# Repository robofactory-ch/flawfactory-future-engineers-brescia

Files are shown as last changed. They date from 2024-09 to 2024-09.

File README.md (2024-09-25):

# FlawFactory

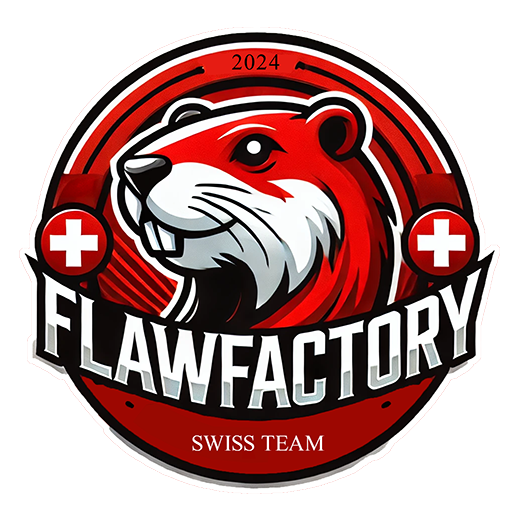
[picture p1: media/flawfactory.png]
FlawFactory Logo






**This is the github repository for team FlawFactory for WRO 2024 Brescia. You'll find our documentation in this readme**

We, Damian Hardegger and Jesse Born, make up the WRO team FlawFactory. We have been taking
part in WRO competitions for several years now. Previously, we competed in di erent teams in the
RoboMission category and were also successful there. But this year we took on a new challenge
and ventured into the Future Engineers task together as a joint team.

## Contents

- [Mobility and Hardware Design](#Mobility-Management)
- [Power and Sense Management](#Power-and-Sense-Management)
  - [Power Management](#Power-Management)
  - [Sense Management](#Sense-Management)
  - [Wiring Diagram](#Wiring-Diagram)
  - [Bill of Materials](#Bill-of-Materials)
- [Obstacle Management](#Obstacle-Management)
- [Photos](#Photos)
- [Videos](#Videos)
- [Enabling Reproducibility](#Enabling-Reproducibility)

<!-- Mobility management discussion should cover how the vehicle movements are managed. What motors are selected, how they are selected and implemented.
A brief discussion regarding the vehicle chassis design /selection can be provided as well as the mounting of all components to the vehicle chassis/structure. The discussion may include engineering principles such as speed, torque, power etc. usage. Building or assembly instructions can be provided together with 3D CAD files to 3D print parts. -->

## Mobility Management

The robot is built on a Lego chassis, which is supplemented where necessary with custom-designed 3D-printed components. These parts securely attach the motors and electronics to the chassis. The Lego structure incorporates dual Ackermann steering mechanism for both axles, allowing the robot to navigate tight turns with ease. To ensure even distribution of rotational power, we integrated a differential gear into each axle, powering all four wheels.

We connected the motors to the chassis using 3D-printed couplings that link the motor shaft directly to a Lego axle, allowing a single DC motor to drive the entire robot. The motor is positioned as low as possible to achieve a stable structure with a low center of gravity. We selected a 12V, 251 RPM motor with a 43.8:1 gearbox, which, despite its modest speed, is ideal for the robot due to its high torque of 18 kg\*cm at a stall current of 7A. This powerful motor allows for smooth driving and acceleration. The steering mechanism utilizes an RC servo motor with a stall torque of 15 kg\*cm, connected to the steering axle via a 3D-printed coupling and Lego gears. Since the DC motor obstructed the direct connection between the front and rear axles for simultaneous steering, we extended the linkage above the motor, placing the servo motor on top of the robot.

For the remaining electronics, we designed and printed additional parts. The camera mount is designed to allow the camera to be easily inserted from the top. The other electronics are mounted on a two-story plate, which is attached to the chassis using the classic Lego method of pushing axles through the 3D-printed parts and beams. We used standard M3 or M2.5 hardware to assemble the 3D-printed components and secure the electronics. The parts were designed to allow nuts to be pressed into place without support structures during printing, enabling a strong and reliable connection. Depending on accessibility, we used either square or hex nuts for the assembly.

<!-- Power and Sense management discussion should cover the power source for the vehicle as well as the sensors required to provide the vehicle with information to negotiate the different challenges. The discussion can include the reasons for selecting various sensors and how they are being used on the vehicle together with power consumption. The discussion could include a wiring diagram with BOM for the vehicle that includes all aspects of professional wiring diagrams. -->

## Power and Sense Management

### Power Management

We utilize a standard 4S LiPo battery as our power source. This versatile, off-the-shelf solution enables us to power both our drive and computer vision subsystems using a DC-DC buck converter. The 14.8V from the battery is directly fed into the H-Bridge motor driver, specifically an L298N variant. The buck converter provides a stable 5V supply to the main onboard computer, a Raspberry Pi 4B, which runs our computer vision algorithms. The 5V output is also routed to an Arduino Nano, connected via USB serial to the Raspberry Pi, to separate vision processing from motor control. The Arduino Nano handles tasks such as acceleration and PWM modulation.

Power consumption was a significant consideration, as the Raspberry Pi can draw up to 1.2 amps, and the servo motor can pull up to 4A in a stall situation. The DC-DC converter was selected to meet these requirements. The drive motor, powered separately, can draw up to 7A. By separating the power sources, only the H-Bridge needed to be rated for these high currents.

Due to cost considerations, we selected an H-Bridge with a current rating below the stall current, necessitating gradual acceleration to avoid damage—a lesson learned through experience. The H-Bridge allows the Arduino Nano to control the motor with three pins: two for selecting the direction of rotation and one for moderating speed using PWM (pulse width modulation). This setup ensures that the 12V system can be safely controlled using the 5V logic from the Raspberry Pi and Arduino.

### Sense Management

For the regional finals, we experimented with various sensors, including ultrasonic sensors, gyroscopes, and cameras. Through our trials, we discovered that a camera alone suffices, provided it has a sufficiently wide field of view. Consequently, we selected a Pi HQ camera equipped with a screw-on lens offering a 120° field of view. This camera allows the robot to accurately perceive its surroundings.

The Pi HQ camera connects directly to the Raspberry Pi, drawing power from the Pi itself, which is supplied via the 5V pins on the GPIO connector. Based on our experiences at the regional finals, we decided to eliminate all ultrasonic sensors and the gyroscope. Instead of relying on hardware sensors, we opted to enhance video processing to emulate distance sensing. To facilitate this and improve wall detection robustness, we mounted the camera precisely 100 mm above the ground, aligning its centerline with the top edge of the walls. This allows us to crop the image to a fixed height, ensuring that the walls are always detected at the same height in the image.

### Wiring Diagram

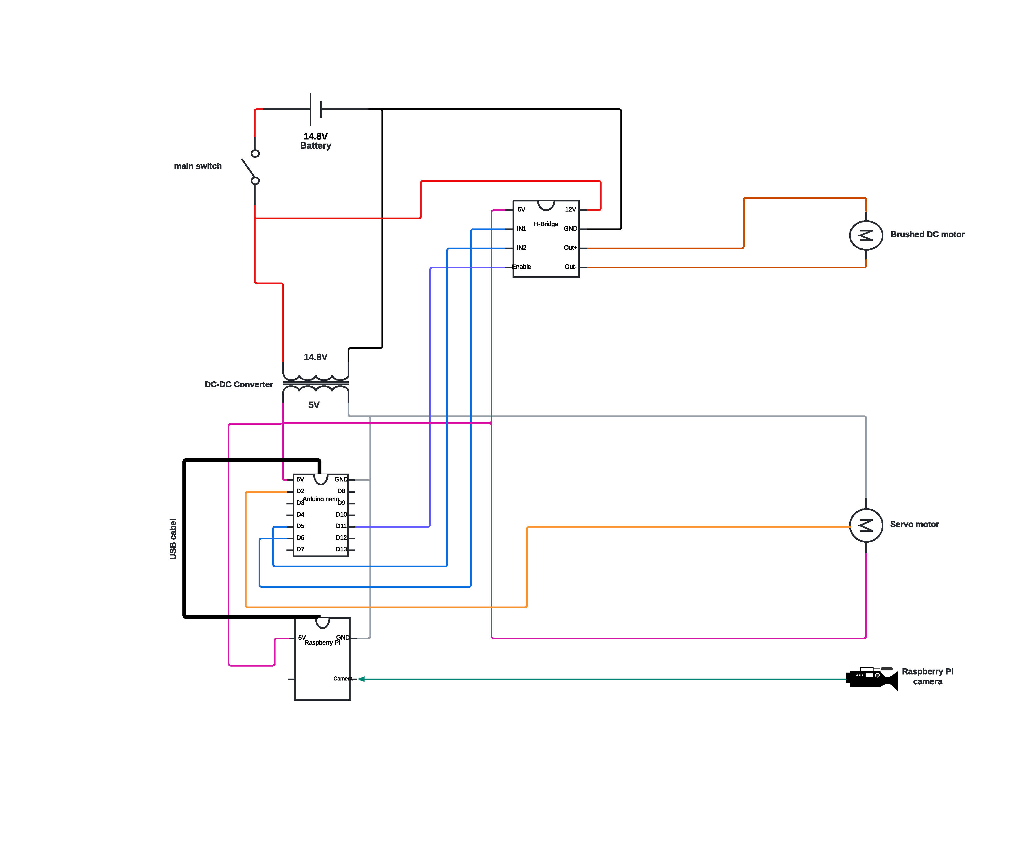
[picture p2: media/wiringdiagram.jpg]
Wiring Diagram


### Bill of Materials

| Amount | Product | Price in Swiss Francs (CHF 1.00 ~ USD 1.18) |
| --- | --- | --- |
| 1 | Raspberry Pi M12 HQ Camera | CHF 45.34 |
| 1 | EDATEC 12MP 3.2mm M12 Raspberry | CHF 28.84 |
| 1 | Raspberry Pi 4 Model B 8GB | CHF 79.00 |
| 1 | Arduino Nano: Multifunktionales Board ATmega328 16Mhz, Mini-USB | CHF 19.95 |
| 1 | Tattu LiPo-Akku 14.8V 850mAh 95C 4S1P RL | CHF 14.00 |
| 1 | L298N Schrittmotorendstufe / H-Brücke / DC Motor Treiber | CHF 8.90 |
| 1 | PDI-5515MG Digital Standard Servo 15.32Kg\*cm | CHF 18.90 |
| 1 | 12V 251RPM 18Kg\*cm DC Getriebemotor mit Encoder | CHF 35.90 |
| ca. 20 pieces | M2.5 Screws and nuts | CHF 2.00 |
| ca. 10 pieces | M2 Screws and nuts | CHF 1.00 |
| ca. 300g | 3D printing filament | CHF 5.00 |
| ca 20 pieces | Jumpercabel | CHF 4.00 |
| See stud.io file | LEGO technic bricks | |
| 4 | LEGO technic wheels | |
| **TOTAL** | | **CHF 262.83** |

<!-- Obstacle management discussion should include the strategy for the vehicle to negotiate the obstacle course for all the challenges. This could include flow diagrams, pseudo code and source code with detailed comments. -->

All files for the 3D printed parts can be found in the [3D-Printed-Parts](/cad/3d) folder. All parts can be printed without supports at 0.2mm layer height. we recommend using PET-G or nGen for the parts (PLA can also be used).
The wiring diagram can be found in the [Wiring Diagram](/media/wiringdiagram.jpg) file. The instructions for the LEGO chassis can be found in the [stud.io file](/cad/future_eng_flawfactory_v2.io).

## Obstacle Management

### Opening Race

The robot's behavior is modeled using a behavior tree. The [StateMachine](/raspy/statemachine.py) class manages the current state and handles transitions to new states. States can also be scheduled to start in the future, which is useful for delaying turns to avoid hitting inner walls. In the opening race, we use the states “STARTING,” “PD-CENTER,” “TURNING-L/R,” and “DONE.”

We begin by determining the round direction. First, we crop the top half of the image and filter out all black pixels using OpenCV's `cv2.inRange` function. On this Boolean map of black pixels, we detect edges using `cv2.Canny`. By applying `np.argmax`, we find the heights of the walls in pixels at each x-coordinate in the image. The discrete differences between these heights are calculated using `np.diff`, raised to the fourth power, and summed up. This helps us identify the jump in wall height when the inner wall first appears.

For driving, we employ a PD-Controller. The input is derived from the black portion of a region-of-interest extracted from the outer edges of the black-and-white Boolean image. This is compared to a pre-calibrated fixed portion. We follow only the outer wall to avoid collisions with the inner walls, especially if their gap distance is randomized to be small.

Using a small region of interest in the center of the camera feed, we detect the blue and orange lines on the game mat. The color image is converted to HSV for this purpose. Upon encountering such a line, depending on its color, we initiate a turn and decrement the remaining corners counter, allowing us to accurately stop at the end of the round.

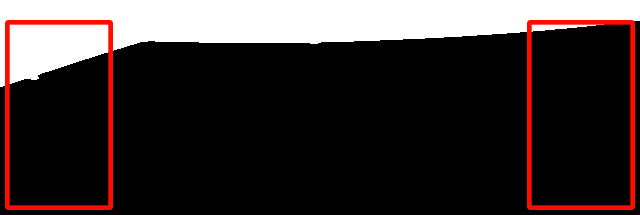
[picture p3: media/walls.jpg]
Wall Detection


The red outlines show the region of interest used for wall detection.

### Obstacle Race

In addition to extracting a black-and-white image, we convert the cropped color image to HSV. This conversion allows us to more easily and robustly extract red and green pixels. We then use `cv2.Canny` and `cv2.findContours` to search for contours in this image. The centroids of the contours are extracted and stored along with their width and height. The behavior tree is updated with two new states: "TRACKING-PILLAR" and "AVOIDING-PILLAR-R/G".

When handling the HSV color space, special care is needed for colors near the red hue due to the wrap-around effect. The hue value for red is around 0° and 360°, meaning it wraps around the HSV color wheel. To accurately detect red, we create two separate masks: one for the lower range (e.g., 0° to 10°) and another for the upper range (e.g., 350° to 360°). These masks are then combined to form a single mask that accurately captures all red hues. This approach ensures that all shades of red are detected, avoiding issues caused by the hue value wrapping around the color wheel.

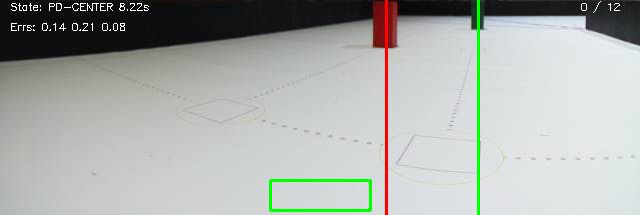
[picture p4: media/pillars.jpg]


In the image above you can see the robot detecting the red and green pillars. After processing the image, the program returns a list of found pillars, sorted by their distance to the robot. The robot then drives towards the closest pillar, until it is close enough to the pillar to avoid it. The robot then drives around the pillar and continues to the next one. You can also see the center ROI used for detecting turn marking lines.

<!-- Insert image with behavior tree here -->

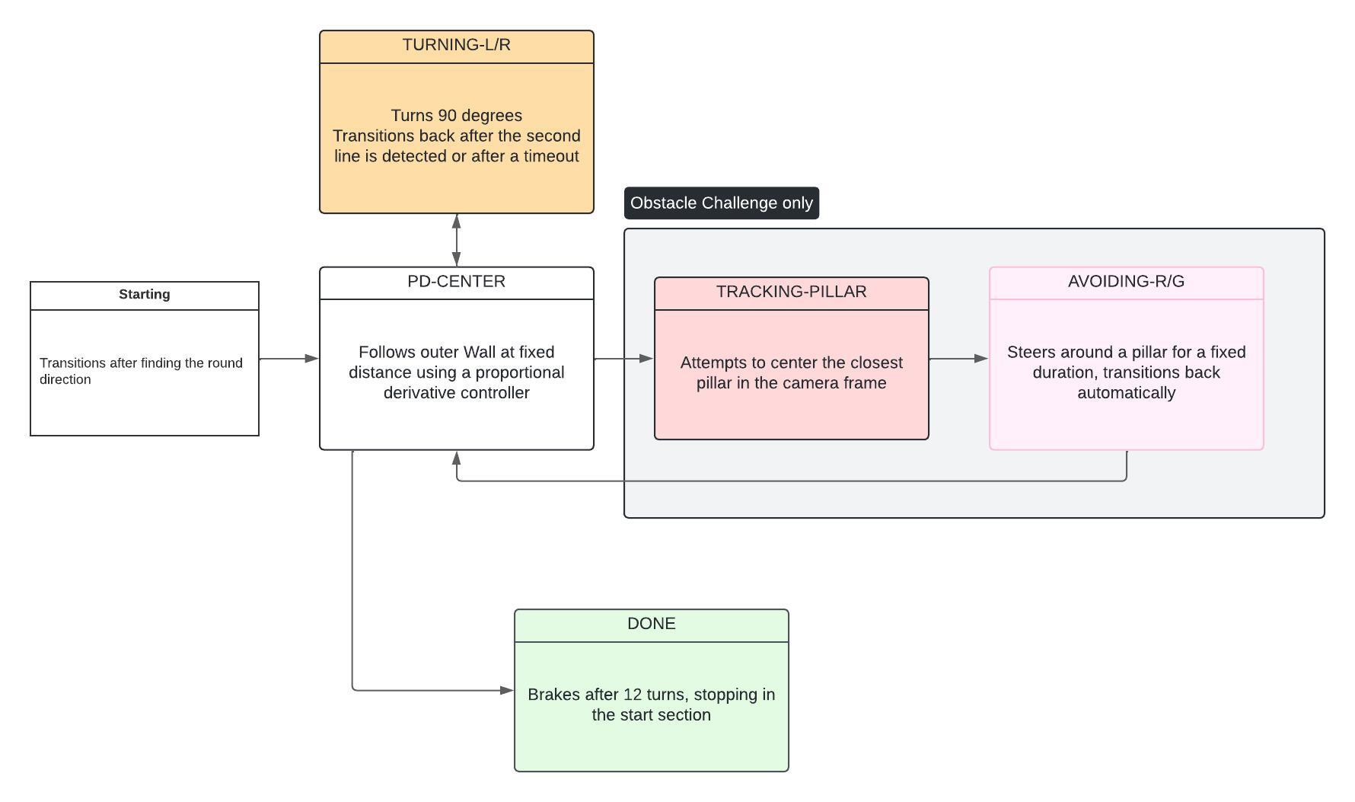
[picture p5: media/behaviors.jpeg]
Behavior Tree


<!-- Pictures of the team and robot must be provided. The pictures of the robot must cover all sides of the robot, must be clear, in focus and show aspects of the mobility, power and sense, and obstacle management. Reference in the discussion sections 1, 2 and 3 can be made to these pictures. Team photo is necessary for judges to relate and identify the team during the local and international competitions. -->

## Photos

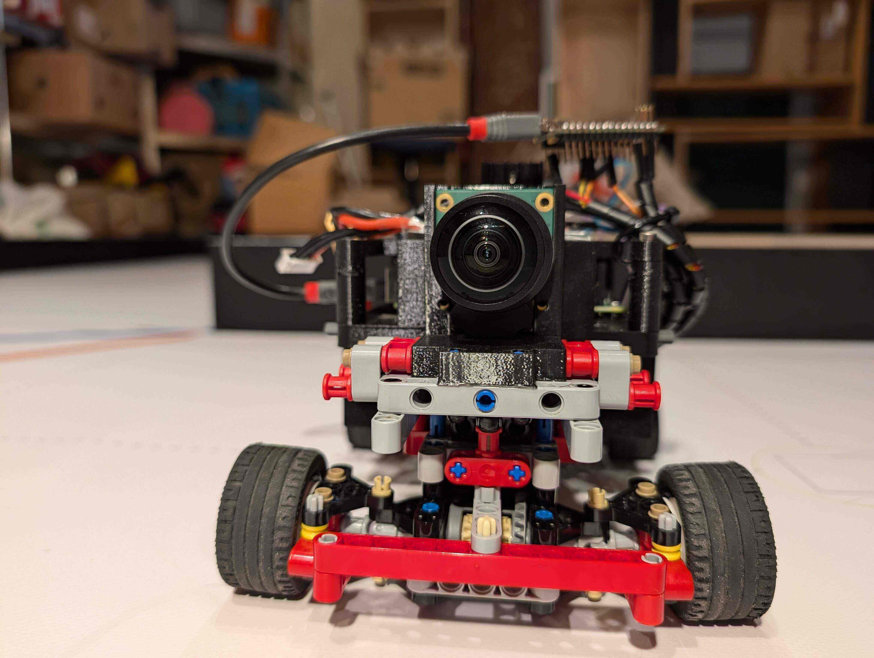
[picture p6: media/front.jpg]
Front
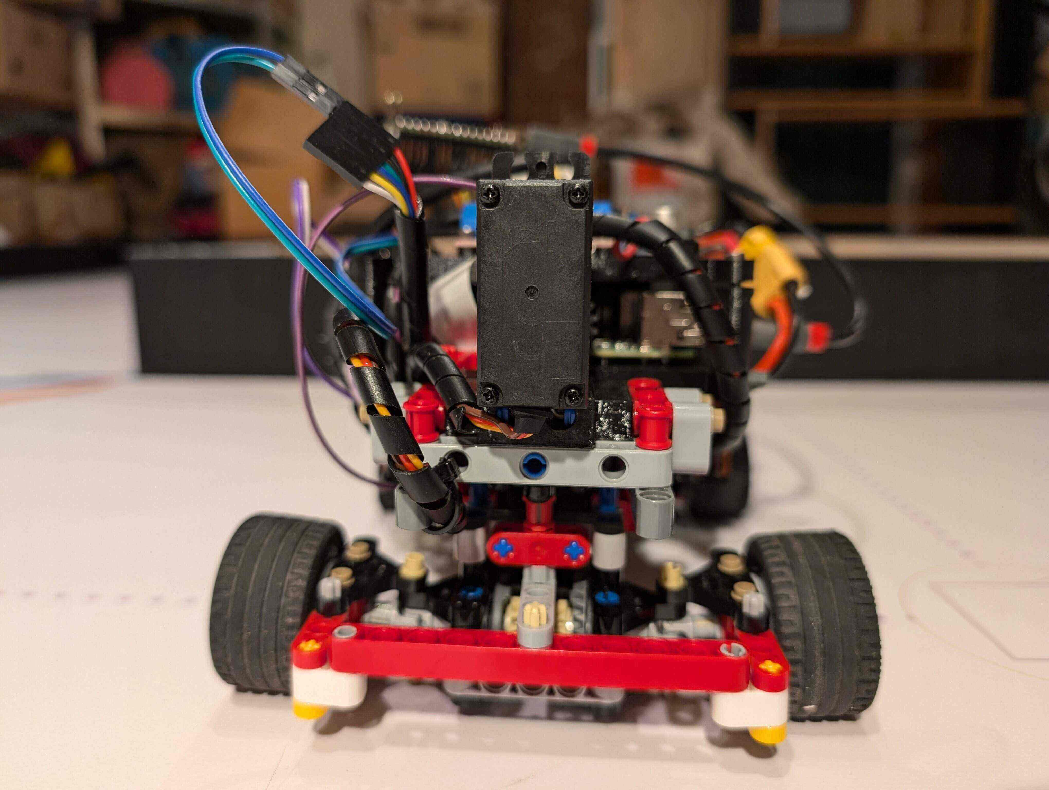
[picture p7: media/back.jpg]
Back
|  |  |
| --- | --- |
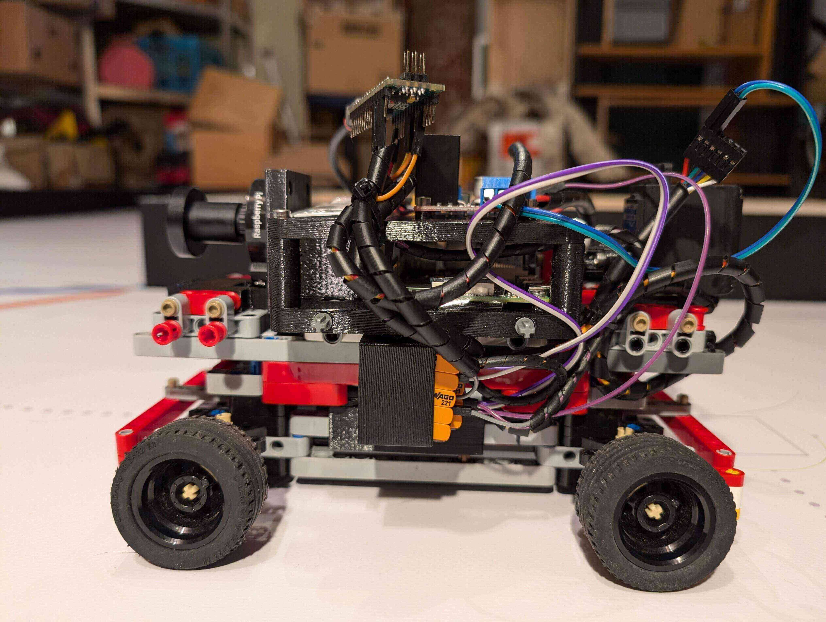
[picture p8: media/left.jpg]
Left
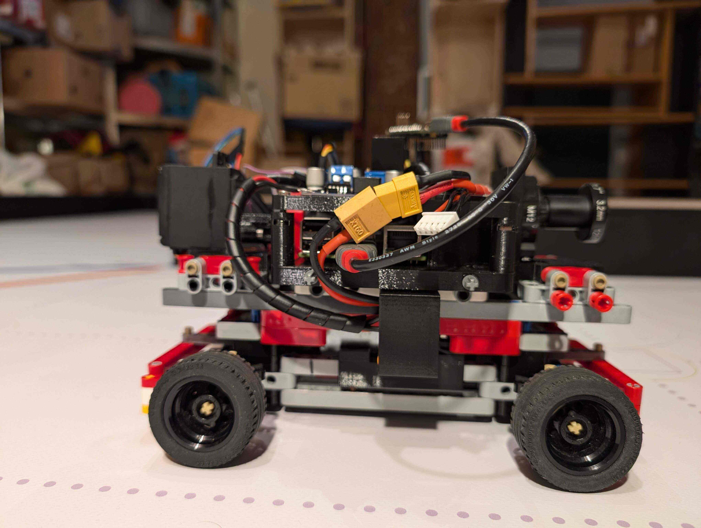
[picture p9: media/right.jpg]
Right
|  |  |
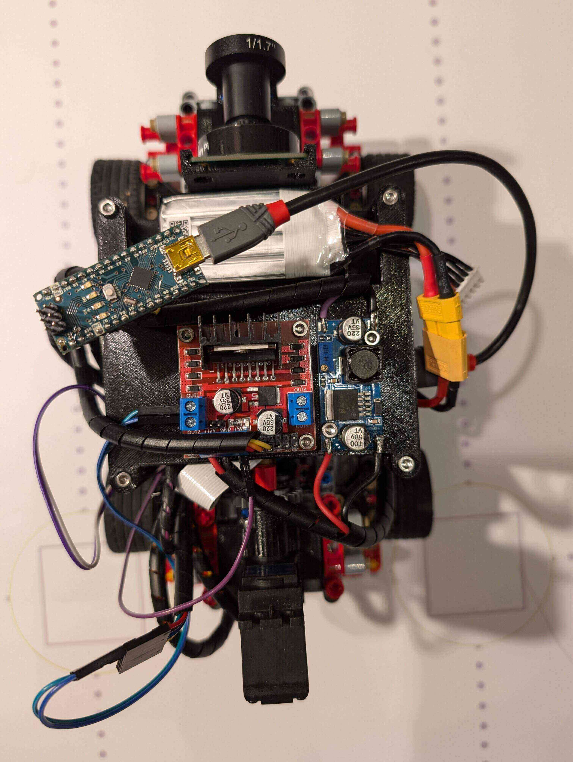
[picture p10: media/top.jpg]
Top
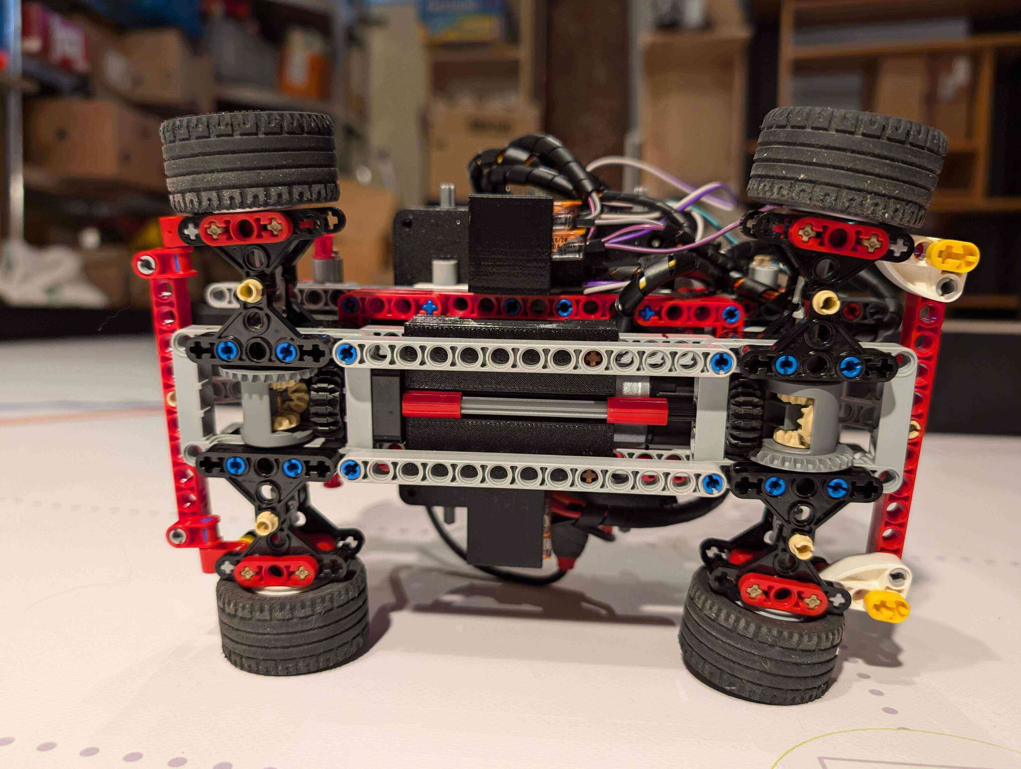
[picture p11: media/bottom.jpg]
Bottom
|  |  |

Team
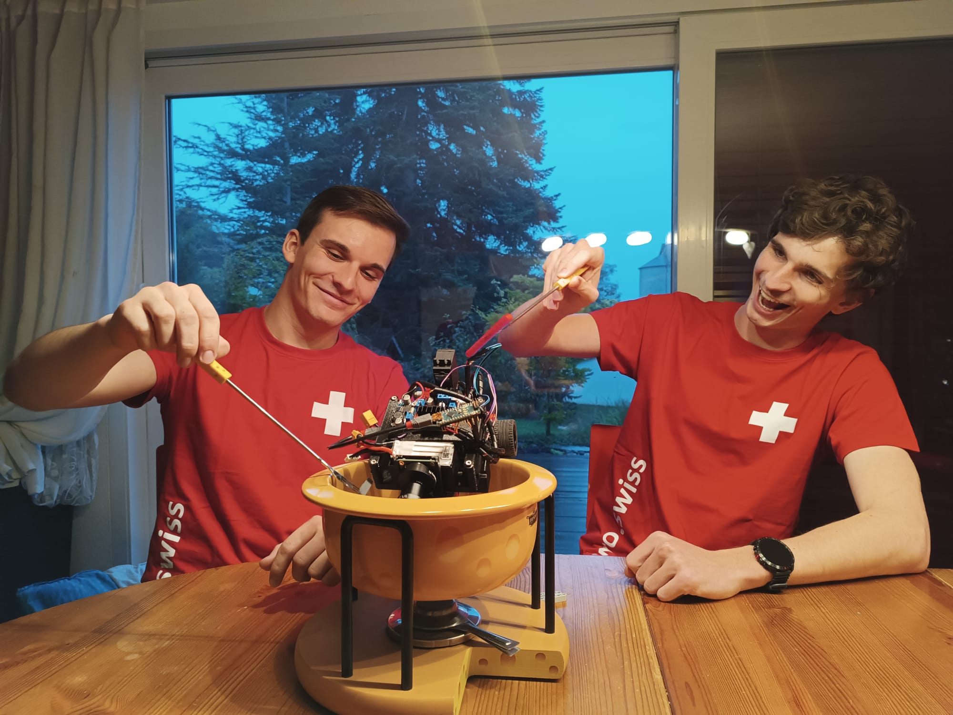
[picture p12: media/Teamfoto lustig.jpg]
Team


**The national menu of Switzerland is fondue. While usually fondue is made from cheese, the team is enjoying a robot fondue 😎🤪**

<!-- The performance videos must demonstrate the performance of the vehicle from start to finish for each challenge. The videos could include an overlay of commentary, titles or animations. The video could also include aspects of section 1, 2 or 3 -->

## Videos

<!-- https://michaelcurrin.github.io/badge-generator/#/generic -->





## Enabling Reproducibility

To enable the reproduction of our robot, we provide the following installation instructions:

1. Install rapsberry pi os on your raspberry pi using the [official guide](https://www.raspberrypi.org/documentation/installation/installing-images/README.md) While the os is installing, you can falsh the arduino code to the arduino nano. The arduino code can be found in the [arduino](/arduino/OutputProxy) folder. The code can be uploaded using platformIO.
2. After booting up the raspberry pi, connect via ssh, and install the following packages:

```bash
sudo apt-get update
sudo apt-get install python3-opencv python3-websockets python3-numpy python3-pyserial
```

3. Enable the camera using `sudo raspi-config` and reboot the raspberry pi for the changes to take effect. Install the corresponding python module:

```bash
sudo apt-get installpython3-picamera2
```

4. Clone the repository and run the main script:

```bash
git clone https://github.com/robofactory-ch/flawfactory-future-engineers-brescia.git
```

5. Running the robot in dev mode

Check in the config file, if the correct usb port is set for the arduino. Check the correct port with `ls /dev/tty*` and look for the port that is connected to the arduino. Change the port in the config file to the correct port.

Make sure pillars are enabled/disabled in the config file, and that no fixed round direction is set.

Navigate to the `raspy` directory and run the main script:

```bash
cd flawfactory-future-engineers-brescia/raspy
python3 roi.py
```

To launch the robot, open the web interface in your browser and start the robot by clicking the connect button. The robot will now start driving autonomously. To stop the robot, you can close the web interface, press the stop button on the robot or press `ctrl+c` in the ssh session.

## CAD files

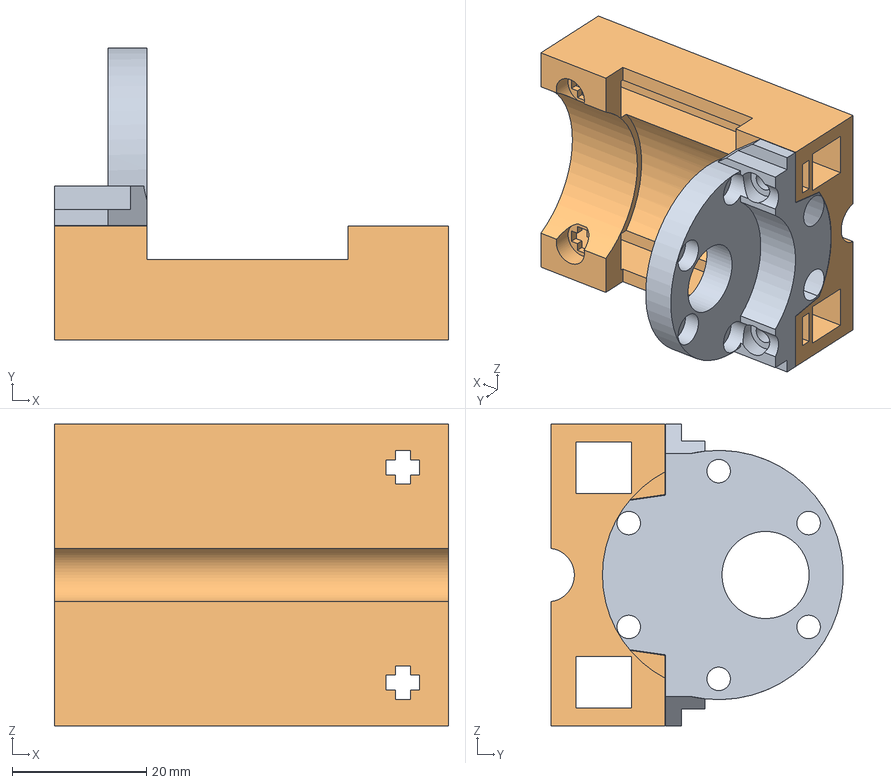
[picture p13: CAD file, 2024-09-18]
cad/3d/Driving Motor Base.step
58.8 x 43.6 x 45.0 mm

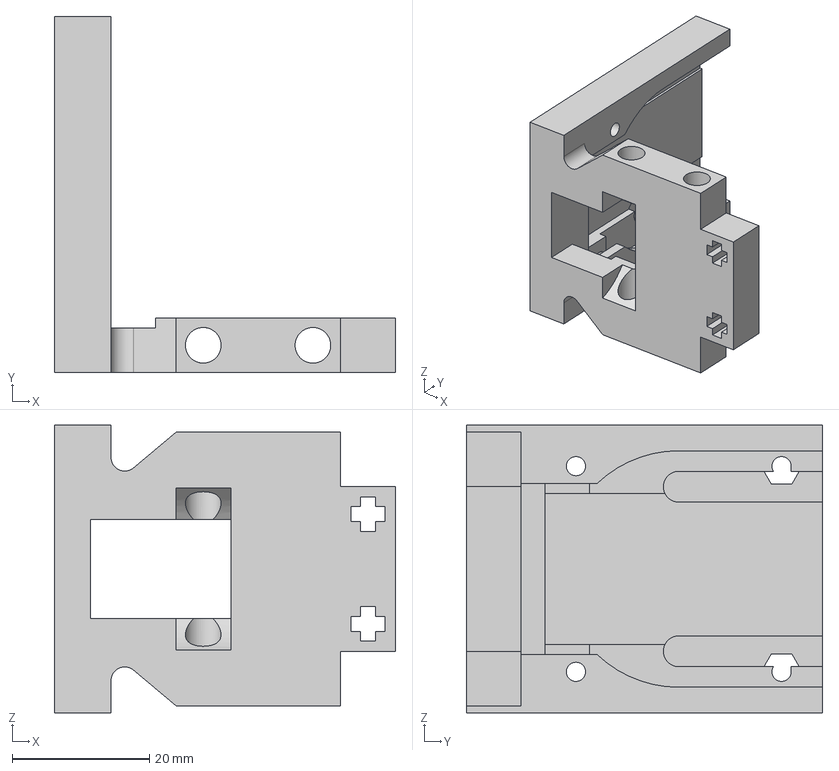
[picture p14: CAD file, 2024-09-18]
cad/3d/Camera mount.step
49.8 x 52.0 x 42.0 mm

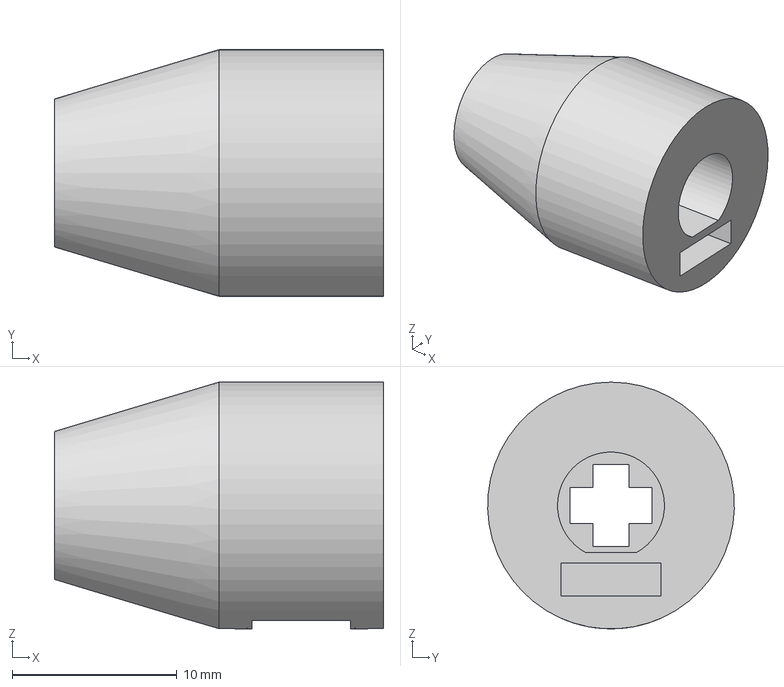
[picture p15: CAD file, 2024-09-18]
cad/3d/Shaft connector.step
20.0 x 15.0 x 15.0 mm

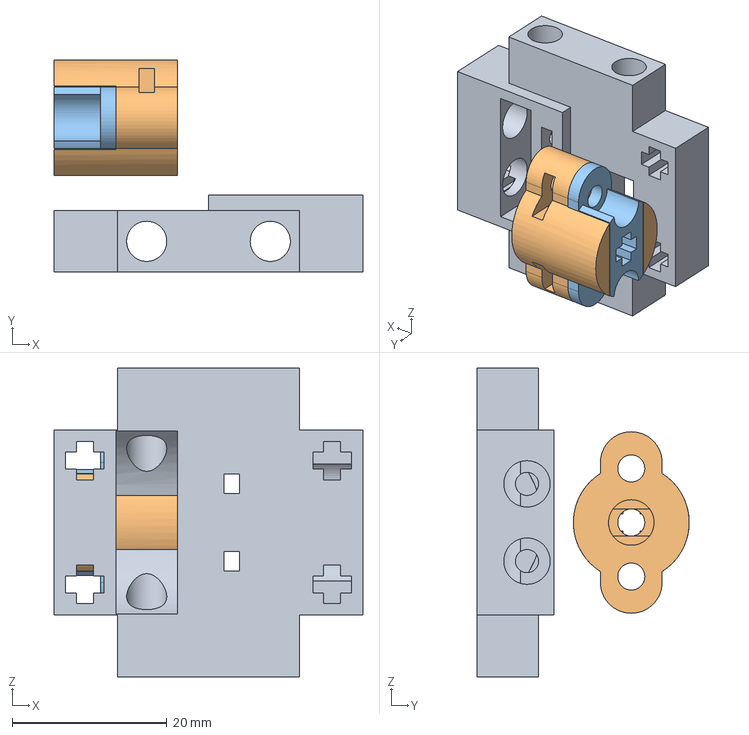
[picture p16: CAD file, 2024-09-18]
cad/3d/Servo mount.step
40.0 x 27.5 x 40.0 mm

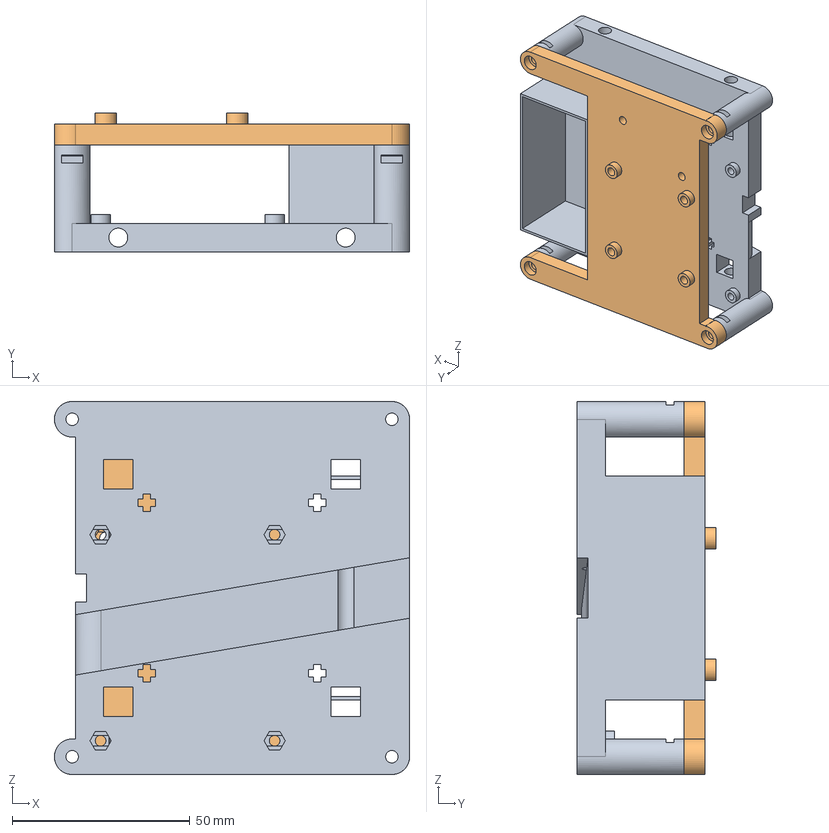
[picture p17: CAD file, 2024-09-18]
cad/3d/Battery and Raspberry mount.step
100.0 x 39.0 x 105.0 mm

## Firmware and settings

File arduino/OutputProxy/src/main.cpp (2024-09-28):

#include <Arduino.h>
#include <Servo.h>

const int servoPin = 2;

Servo servo;

const int enaPin = 11;
const int in1Pin = 5;
const int in2Pin = 6;

const int enTogglePin = 7;

bool en_state = false;

int current_speed = 0;
int set_speed = 0;
unsigned long acc_time = 20;
unsigned long last_acc_time = 0;

int middle = 70; // +55 -55
int degree_max = 125;
int degree_min = 15;
int current_degree = 0;
int set_degree = 0;

#define BUFFER_SIZE 64

char ringBuffer[BUFFER_SIZE];
int head = 0;
int tail = 0;

void drive(int speed)
{
  if (speed > 200)
  {
    speed = 200;
  }
  else if (speed < -200)
  {
    speed = -200;
  }
  if (millis() < last_acc_time + acc_time)
  {
    return;
  }
  last_acc_time = millis();
  if (abs(speed - current_speed) > 1)
  {
    current_speed = current_speed + (speed - current_speed) / fabs(speed - current_speed) * 1;
  }
  else if (speed == 0)
  {
    current_speed = 0;
  }
  if (current_speed > 0)
  {
    digitalWrite(in1Pin, LOW);
    digitalWrite(in2Pin, HIGH);
  }
  else if (current_speed < 0)
  {
    digitalWrite(in1Pin, HIGH);
    digitalWrite(in2Pin, LOW);
  }
  else
  {
    digitalWrite(in1Pin, LOW);
    digitalWrite(in2Pin, LOW);
  }
  analogWrite(enaPin, abs(current_speed));
}

void steer(int angle)
{
  angle = angle + middle;
  if (angle > degree_max)
  {
    angle = degree_max;
  }
  else if (angle < degree_min)
  {
    angle = degree_min;
  }
  servo.write(angle);
}

void parseMessage(char *msg)
{
  char cmd[3]; // To store the 2-char command
  int value = 0;

  sscanf(msg, "%1s", cmd);

  // skip whitespace
  char *beg = ++msg;

  while (*beg == ' ')
  {
    beg++;
  }

  char *end = beg;

  while (*end != '\0')
  {
    end++;
  }

  // Serial.println(cmd);
  value = atoi(beg);
  // Serial.println(value);

  if (cmd[0] == 'd')
  {
    set_speed = value;
  }
  else if (cmd[0] == 's')
  {
    set_degree = value;
  }
}

void processMessage()
{
  // Message extraction from ring buffer
  char message[BUFFER_SIZE];
  int index = 0;
  while (tail != head)
  {
    char currentChar = ringBuffer[tail];
    tail = (tail + 1) % BUFFER_SIZE;

    if (currentChar == '\n')
    { // End of message
      break;
    }

    message[index++] = currentChar;
  }

  message[index] = '\0'; // Null-terminate the message string
  // Serial.println(message);

  // Parse the extracted message
  parseMessage(message);
}

void checkEnable()
{
  bool last_state = en_state;
  en_state = digitalRead(enTogglePin) == HIGH;

  if (en_state != last_state)
  {
    if (en_state)
    {
      Serial.println("enable 1");
    }
    else
    {
      Serial.println("enable 0");
    }
    delay(250);
  }
}

void setup()
{
  pinMode(in1Pin, OUTPUT);
  pinMode(in2Pin, OUTPUT);

  pinMode(enTogglePin, INPUT);

  servo.attach(servoPin);

  digitalWrite(in1Pin, LOW);
  digitalWrite(in2Pin, LOW);
  analogWrite(enaPin, 0);
  Serial.begin(9600);
}

int a = 0;

void loop()
{
  while (Serial.available() > 0)
  {
    char incomingByte = Serial.read();
    // Serial.print(incomingByte);
    ringBuffer[head] = incomingByte;
    head = ++head % BUFFER_SIZE; // Move the head and wrap it around

    // If head meets tail, it means buffer overflow, so move tail forward
    if (head == tail)
    {
      tail = ++tail % BUFFER_SIZE;
    }

    // Check for the end of the message (newline '\n')
    if (incomingByte == '\n')
    {
      processMessage();
    }
  }
  steer(en_state ? set_degree : 0);
  drive(en_state ? set_speed : 0);
  checkEnable();
}

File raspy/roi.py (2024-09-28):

import asyncio
import base64
import json
import math
import os
from time import sleep
import cv2
import numpy as np
import serial
import serial.tools.list_ports
from websockets import WebSocketServerProtocol, serve
from config import ConfigLoader
from helpers import Pillar, extract_ROI
from pipeline import Pipeline
from statemachine import StateMachine
from picamera2 import Picamera2
from rounddir import find_round_dir
import argparse

#?: Webviewer controls for tuning colors, pd, and selecting stream

configloader = ConfigLoader("config.json")
pipeline = Pipeline(configloader)

picam2 = Picamera2()
picam2.configure(picam2.create_preview_configuration())
picam2.start()

picam2.set_controls({
    "AwbEnable": False,
    # controls.AWB_TEMPERATURE: fixed_temperature
})



ports = serial.tools.list_ports.comports()


try:
  ser = serial.Serial(configloader.get_property("ArduinoSerialPort"), 9600)
except:
  print("Arduino not connected, available devices")
  ser = None
  for port, desc, hwid in sorted(ports):
        print("{}: {} [{}]".format(port, desc, hwid))

def cycle():
  global sm, last_error, kp, kd

  # image reading, usually form camera
  img = cv2.cvtColor(picam2.capture_array(), cv2.COLOR_RGB2BGR)
  
  # undistorted = pipeline.undistort(img)
  color_image = pipeline.crop(img)

  # copy for webviewer visualization
  viz = color_image.copy()

  # convert to hsv, for color filtering
  hsv_image = cv2.cvtColor(color_image, cv2.COLOR_BGR2HSV)

  # center region-of-interest for detecting the turn marker lines
  roi_center_w, roi_center_h = 100, 30
  roi_center_x, roi_center_y = 320 - roi_center_w // 2, 180
  cv2.rectangle(viz, (roi_center_x, roi_center_y), (roi_center_x + roi_center_w, roi_center_y + roi_center_h), (0, 255, 0), 2)
  roi_center = extract_ROI(hsv_image, [roi_center_x, roi_center_y], [roi_center_x + roi_center_w, roi_center_y + roi_center_h])
  
  # filter out the orange and blue colors of turn markers
  orange_blue = pipeline.filter_OB(roi_center)
  rgbl = pipeline.filter_RG_Bl(hsv_image, color_image)

  # how much orange/blue is in the center region-of-interest?
  portion_orange = cv2.countNonZero(orange_blue["orange"]) / (orange_blue["orange"].shape[0] * orange_blue["orange"].shape[1])
  portion_blue = cv2.countNonZero(orange_blue["blue"]) / (orange_blue["blue"].shape[0] * orange_blue["blue"].shape[1])


  # l and r ROIs used for PD control, to keep the car in the middle of the track and away from walls
  roi_width = 100
  roi_left = extract_ROI(rgbl["black"], [0, 0], [roi_width, 150])
  roi_right = extract_ROI(rgbl["black"], [640-roi_width, 0], [640, 150])

  portion_black_l = cv2.countNonZero(roi_left) / (roi_left.shape[0] * roi_left.shape[1])
  portion_black_r = cv2.countNonZero(roi_right) / (roi_right.shape[0] * roi_right.shape[1])

  # print("err:", portion_black_l-portion_black_r,"left: ", portion_black_l, "right: ", portion_black_r)

  # filter out the red and green colors of the pillars and walls
  pillars_r = pipeline.get_pillars(rgbl["red"], "RED")
  pillars_g = pipeline.get_pillars(rgbl["green"], "GREEN")
  pillars = pillars_r + pillars_g

  pillars.sort(key=lambda x: x.width*x.height, reverse=True)

  # check if the next pillar is before or after a turn marker
  if len(pillars) > 0:
    next_pillar = pillars[0]
    next_pillar.width = min(next_pillar.width, 5)
    # for this extract a region-of-interest around the pillar
    roi_pillar_check = extract_ROI(hsv_image, [next_pillar.screen_x - int(next_pillar.width*0.35), 0], [next_pillar.screen_x + int(next_pillar.width*0.35), hsv_image.shape[1]])
    # filter out the orange and blue colors

    # print("A=", pillars[0].width * pillars[0].height)

    if not roi_pillar_check.shape[0] == 0 and not roi_pillar_check.shape[1] == 0:
      orange_blue_pillar = pipeline.filter_OB(roi_pillar_check)
      portion_orange_pillar = cv2.countNonZero(orange_blue_pillar["orange"]) / (orange_blue_pillar["orange"].shape[0] * orange_blue_pillar["orange"].shape[1])
      portion_blue_pillar = cv2.countNonZero(orange_blue_pillar["blue"]) / (orange_blue_pillar["blue"].shape[0] * orange_blue_pillar["blue"].shape[1])
      # check if the pillar is before or after a turn marker
      # print("pillar check", portion_orange_pillar, portion_blue_pillar)
      if portion_orange_pillar > 0.00005 or portion_blue_pillar > 0.00005:
        # print("Pillar is after a turn marker")
        pillars[0].ignore = True
      
  # A state machine is used to model the car's behavior
  # This checks if the car should transition to a new state, and if so, transitions
  # states may be PD-CENTER, PD-RIGHT, PD-LEFT, TURNING-L, TURNING-R, etc.
  transition_res = sm.shouldTransitionState(portion_orange, portion_blue, pillars)
  if transition_res:
    print(f"Transitioning to {sm.current_state}")

  # PD control

  # This is the reference value for the single side PD control, 
  # eg. how much black should be on the left side when the car follows the left outer wall

  # pillar_ref = 0.35
  # if sm.next_pillar:
  #   if sm.next_pillar.ignore:
  #     pillar_ref = 0.48
    

  REF_PORTION = 0.45 if not sm.isPillarRound else 0.45

  # error value
  error = 0.0

  turn_correction = 0.75 if not sm.isPillarRound else 1.0

  PD_STATES = ["PD-CENTER", "PD-RIGHT", "PD-LEFT"]

  if sm.current_state == "TRACKING-PILLAR" and len(pillars) > 0:
    # attempt to keep the pillar in the center of the image
    error = float(pillars[0].screen_x - 320) / 640.0

  # follow the left wall, if we're going counter-clockwise
  if sm.current_state in PD_STATES and sm.round_dir == -1:
    error = REF_PORTION - portion_black_r

  # follow the right wall, if we're going clockwise
  if sm.current_state in PD_STATES and sm.round_dir == 1:
    error = portion_black_l - REF_PORTION


  correction = error * kp + (error - last_error) * kd

  
  if sm.current_state == "TURNING-L":
    correction = -turn_correction
  if sm.current_state == "TURNING-R":
    correction = turn_correction
  
  FIRSTPAHSETIME = 0.95
  # if len(pillars) > 0:
  #   if sm.avoid_big or True:
  #     FIRSTPAHSETIME = 1.2

  if (sm.current_state == "AVOIDING-R" and sm.time_diff < FIRSTPAHSETIME):
    correction = 0.9
  if (sm.current_state == "AVOIDING-G" and sm.time_diff > FIRSTPAHSETIME):
    correction = 0.9*0.9
  if (sm.current_state == "AVOIDING-G" and sm.time_diff < FIRSTPAHSETIME):
    correction = -0.9
  if (sm.current_state == "AVOIDING-R" and sm.time_diff > FIRSTPAHSETIME):
    correction = -0.9*0.9

  if sm.current_state == "DONE":
    correction = 0.0
    print("---- DONE ----")
    if ser:
      message = "d" + str(int(0)) + "\n"
      ser.write(message.encode())
      message = "s0\n"
      ser.write(message.encode())
    # exit()
    sleep(5)
    exit()

  if sm.search_for_dir and sm.current_state == "STARTING":
    sm.round_dir += find_round_dir(black_img=rgbl["black"])

  
  # else:
  #   correction = 0.0
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

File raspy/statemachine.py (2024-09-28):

from fftime import time

from helpers import Pillar

class StateMachine:

  current_state = "STARTING"
  last_state_time = 0.0
  round_dir = 0
  turns_left = 12

  time_diff = 0.0

  search_for_dir = True

  _scheduled_state = None
  _time_last_avoid = -5

  _scheduled_state_block = False

  next_pillar = None

  first_line_found = None

  avoid_big = False

  def __init__(self, isPillarRound: bool = False) -> None:
    self.last_state_time = time()
    self.isPillarRound = isPillarRound

  def transitionState(self, new_state: str):
    self.current_state = new_state
    self.last_state_time = time()
  
  def scheduleStateTransition(self, new_state: str, time_diff: float, block=True):
    self._scheduled_state = (new_state, time() + time_diff)
    self._scheduled_state_block = block

  def shouldTransitionState(self, portion_orange: float, portion_blue: float, pillars: list[Pillar]):
    time_diff = time() - self.last_state_time
    self.time_diff = time_diff

    if self._scheduled_state is not None:
      new_state, scheduled_time = self._scheduled_state
      if time() > scheduled_time:
        print("Scheduled state transition to", new_state)
        self.transitionState(new_state)
        self._scheduled_state = None
        return True
      if self._scheduled_state_block:
        return False
    
    if self.current_state == "STARTING":
      if abs(self.round_dir) > 10:
        self.round_dir = 1 if self.round_dir > 0 else -1
        self.search_for_dir = False
        self.transitionState("PD-CENTER")
        return True
      else:
        self.search_for_dir = True
        return False


    if self.current_state == "PD-CENTER" and self.turns_left <= 0 and self._scheduled_state is None:
      self.scheduleStateTransition("DONE", 3.1, False)
      return True
    
    # Hold the current state for a minimum of x seconds
    HOLD_STATES = [["TURNING-L", "TURNING-R", "PD-CENTER"]]
    if self.current_state in HOLD_STATES and time_diff < 0.4:
      return False
    
    if len(pillars) > 0 and self.isPillarRound:
      # Pillars are already sorted by distance, as their projected size is proportional to their distance
      next_pillar = pillars[0]
      # print("Next pillar:", next_pillar.color, "height:", next_pillar.height)
      if self.current_state == "PD-CENTER":
        self.next_pillar = next_pillar
        if next_pillar.height*next_pillar.width > 190 and (not next_pillar.ignore):
          self.transitionState("TRACKING-PILLAR")
          return True
      elif self.current_state == "TRACKING-PILLAR" or self.current_state == "PD-CENTER":
        if next_pillar.height*next_pillar.width > 530 and (time() - self._time_last_avoid) > 1.0:
          # self._time_last_avoid = time()
          self.transitionState(f"AVOIDING-{'R' if next_pillar.color == 'RED' else 'G'}")
          self.next_pillar = None
          return True

    if self.current_state == "TRACKING-PILLAR":
      # HOW?? Pillars has been lost, tracking is no more
      if len(pillars) == 0:
        print("Lost the pillar, tracking aborted")
        self.transitionState("PD-CENTER")
        return True

    if self.current_state == "AVOIDING-R" or self.current_state == "AVOIDING-G":
      if time_diff > 2.5: # Avoid for 0.6 seconds, huck and pray
        self.transitionState("PD-CENTER")
        self._time_last_avoid = time()
        self.avoid_big = False
        return True
    

    # We always finnish a turn after this timeout, no matter what. 
    # PD shall deal with straightening out
    TURN_TIMEOUT = 0.85
    if self.current_state in ["TURNING-L", "TURNING-R"]:
      if time_diff > TURN_TIMEOUT:
        self.transitionState("PD-CENTER")
        return True
      return False
    
    # If we run up on a turn marker, we should turn in the corresponding direction.
    # If we are already turning, and we see the other color, 
    # we should stop turning and straighten out with PD
    MIN_PORTION = 0.25
    if portion_blue > MIN_PORTION:
      if self.current_state != "TURNING-R" and self.round_dir < 0:
        self.turns_left -= 1
        if self.isPillarRound:
          # to = 0.45
          # if self.next_pillar:
          #   is_outer = (self.next_pillar.color == "RED" and self.round_dir == -1) or (self.next_pillar.color == "GREEN" and self.round_dir == 1)
          #   self.scheduleStateTransition("TURNING-L", 0.7 if is_outer else 0.2)
          # else:
            self.scheduleStateTransition("TURNING-L", 0.3)
        else:
          self.scheduleStateTransition("TURNING-L", 0.7 if not self.isPillarRound else 0.45)
      else:
        self.transitionState("PD-CENTER")
      return True
    
    if portion_orange > MIN_PORTION:
      if self.current_state != "TURNING-L" and self.round_dir > 0:
        self.turns_left -= 1
        if self.isPillarRound:
          # to = 0.45
          # if self.next_pillar:
          #   is_outer = (self.next_pillar.color == "RED" and self.round_dir == -1) or (self.next_pillar.color == "GREEN" and self.round_dir == 1)
          #   self.scheduleStateTransition("TURNING-R", 0.7 if is_outer else 0.2)
          # else:
            self.scheduleStateTransition("TURNING-R", 0.3)
        else:
          self.scheduleStateTransition("TURNING-R", 0.7 if not self.isPillarRound else 0.45)
      else:
        self.transitionState("PD-CENTER")
      return True
    
      
    return False

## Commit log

2024-09-08 basic functions for arduino nano
2024-09-08 Refactor Arduino code for improved motor control and message parsing
2024-09-18 add BOM
2024-09-18 better print desc
2024-09-18 3d files
    [Battery and Raspberry mount.step, Camera mount.step, Driving Motor Base.step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]
2024-09-18 arduino nano code
2024-09-19 respect unconnected servo
2024-09-23 fix empty mat in pillar after line check
    [roi.py]
2024-09-23 fix frame empty check and
    [roi.py]
2024-09-24 add start button
2024-09-28 debounce enable switch
2024-09-28 emergency stop on arduino
2024-09-28 fix rounddir for the 6th time
    [rounddir.py]
